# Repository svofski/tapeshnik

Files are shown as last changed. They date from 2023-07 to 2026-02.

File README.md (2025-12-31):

# Tapeshnik

Compact cassette data drive.

Project goals. Not all of them are realistic.

  * utilize an existing consumer tape mechanism with "logic control" to make a fully automatic tape drive
  * investigate the limits of what can be done with a simple compact cassette
  * implement random access to sectors
  * a usb mass storage device
  * use a stereo track for double data rate access, eventually use a 4-track head for quad data rate
  * investigate if altering motor speed to improve r/w speeds makes sense
  * investigate feasibility of reading while fast-forwarding with heads half-lifted

Eventually it's doomed to become either a dust gatherer/conversation piece or an art installation.

# Notes

There is no blog, but there are project notes, updated sometimes: [NOTES](docs/NOTES.md)

Note on the second iteration of Tapeshnik: [FUTURISTIC](docs/FUTURISTIC.md)

There is also a [youtube playlist](https://www.youtube.com/playlist?list=PLuOXWyWDhULNxkAvCRtwkEgnuxFfULnF9), where I try to show noteworthy things about this project. Like/subscribe!

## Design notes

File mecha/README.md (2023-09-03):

Mecha
~~~~~

This is an attempt to create a custom tape transport using available off the shelf parts, PCBs and 3d printed parts.

Useful projects and stuff
~~~~~~~~~~~~~~~~~~~~~~~~~

#### Mouse sensor PMW3389DM-T3QU + LM19-LSI

Breakout board https://github.com/siderakb/pmw3360-pcb

SROM
https://github.com/dkao/Kensington_Expert_Mouse_PMW3389_Arduino/blob/master/PMW3389DM-Mouse/SROM_PMW3389.ino

Recommended mouse sensors 
https://thegamingsetup.com/gaming-mouse/buying-guides/flawless-mouse-sensor-list

#### NopSCADlib mechanical parts for OpenSCAD

https://github.com/nophead/NopSCADlib

#### MG90S Servo Model

https://www.thingiverse.com/thing:253557

CAD files
~~~~~~~~~

Used cassette.step by Kai https://grabcad.com/kai-28. I adjusted Kai's design to match real world dimensions, hopefully.

There is no proper OpenSCAD model, although some parts are made using OpenSCAD before importing them into Blender. It's a complete mess that unfortunately can't be helped. Some mechanical OpenSCAD models use NopSCADlib.

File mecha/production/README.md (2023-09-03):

Files for printing

  bracket-l.stl			top cassette bracket left
  bracket-r.stl			top cassette bracket right
  narrow_flange.stl		flange for LM4UU bearing
  rear-bracket.stl		back bracket
  servobracket.stl		MG90S holding bracket
  spindle.stl			cassette spindle

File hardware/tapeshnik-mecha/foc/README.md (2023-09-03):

# TAPESHNIK MOTOR CONTROL

This is a dual-BLDC controller aimed at spinning two BLDC motors of a tape transport.

It is designed with SimpleFOC in mind.

Big thanks to SimpleFOC community for support, reviews and inspiration!

  Controller: 				Waveshare RP2040-Zero
  Motor drivers: 			STSPIN233
  Tape speed sensor:			PMW3389

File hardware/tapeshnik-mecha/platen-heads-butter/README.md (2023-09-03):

# TAPESHNIK Heads-Butter Platen

This is platen #3. The butter of the heads assembly sandwich.

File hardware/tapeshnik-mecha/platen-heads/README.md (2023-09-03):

# TAPESHNIK-MECHA Heads Platen

This is platen #2 of the TAPESHNIK-MECHA.

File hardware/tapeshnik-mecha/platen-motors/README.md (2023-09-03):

# TAPESHNIK Platen-Motors

This is platen #1 of TAPESHNIK-MECHA. It has the motors and the motor control board mounted behind them.

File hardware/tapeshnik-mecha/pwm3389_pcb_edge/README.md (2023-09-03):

# PWM3389-TAPESHNIK

This is a PWM3389 adapter board for use in TAPESHNIK. It is not intended for a general purpose mouse implementation.

The design is based on SideraKB's PMW3360-PCB https://github.com/siderakb/pmw3360-pcb

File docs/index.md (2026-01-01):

# TAPESHNIK 

Tapeshnik is a series of experiments with Compact Cassette tapes using a mix of traditional and modern technologies with focus on data storage.

## Iteration 1

Iteration 1 uses a purchased single-motor mechanism with a command wheel logic control. 
Read/Write circuitry is heavily based on Commodore datasette. Pi Pico is the microcontroller that does logic level data encoding/decoding and deck control functions.

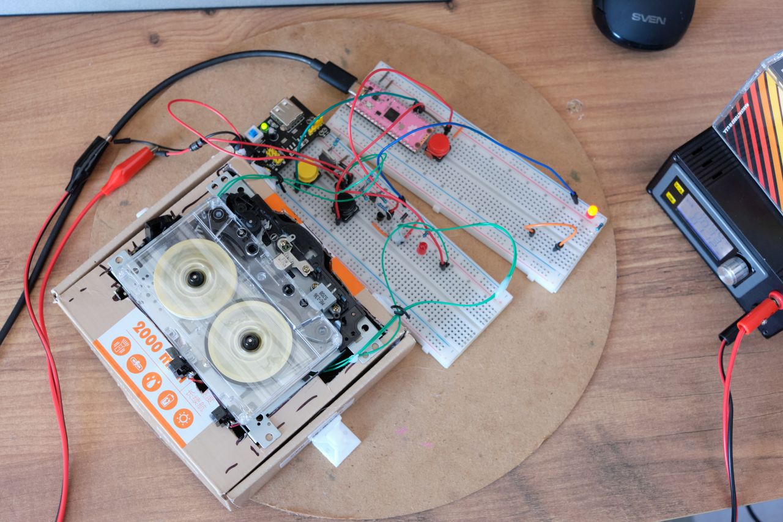
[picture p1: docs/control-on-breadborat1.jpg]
breadborat1


[Iteration 1 Notes](NOTES.md)

It was a moderate success, but not a breakthrough in data storage.

## Iteration 2

I always liked the idea of drives without rubber belts. Making a precision mechanism with a capstan can be a very demanding task. 
Some old data drives used to have no capstan, for example:

 * [Digital TU56 Dectape](https://gunkies.org/wiki/TU60_DECasetteTape_Transport)
 * [Digital TU60 DECassette](https://gunkies.org/wiki/TU60_DECasetteTape_Transport)
   * [Detailed description, principle of operation, data format of TU60](https://bitsavers.org/pdf/dec/decCassette/DEC-00-HTU60-C-D_TU60maint_Oct73.pdf)
 * Coleco Adam Digital Data Pack
 * [D/CAS drives](https://en.wikipedia.org/wiki/D/CAS)
 
Some of them use pre-recorded timing servo track, others appear to use robust encodings that let them recover data despite high tape speed variations.

This gave me ideas for a new experiment with building a fully custom deck without capstan.

mecha2025-2

This is currently a work in progress.

[Iteration 2 "FUTURISTIC" Notes](FUTURISTIC.md)

[youtube playlist](https://www.youtube.com/playlist?list=PLuOXWyWDhULNxkAvCRtwkEgnuxFfULnF9)

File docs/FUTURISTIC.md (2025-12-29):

# Tapeshnik Futuristic Notes

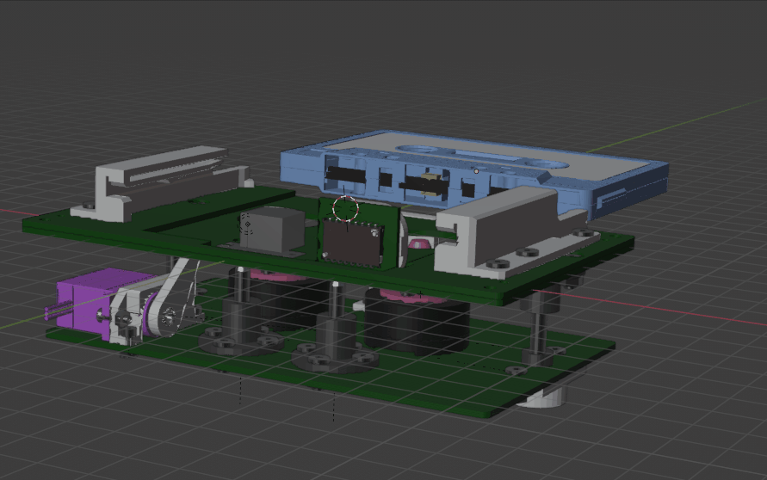
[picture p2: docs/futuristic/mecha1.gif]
mecha


While the current mechanism works, its limitations are obvious and its reliability is questionnable. Shall something break, it will be getting harder to get a replacement.

As a tangent project, I have an idea to design a simple, relatively easy to repeat tape mechanism that could be built from scratch using available parts. Obviously the heads will still have to be sourced, but cassette heads are relatively abundant.

As an inspiration I have TEAC D/CAS system. It uses tapes that look almost identical to Compact Cassettes. It's a two-motor direct drive system without a capstan. 

In D/CAS like TEAC MT-2ST, tape speed is closed-loop controlled by a closed loop servo, formed by the takeup reel motor and tape speed sensor. The tape speed sensor is not unlike a pinch roller, except that it does not pinch, instead rotates by friction with tape and provides speed reading.

Stable tape speed is useful, but depending on method of writing it may be not required. For example, a good PLL on FM or differential manchester can recover +-5% speed variation without issue, probably more with extra tweaks. But even better, if we sacrifice one of the tracks to reference clock signal, tape speed becomes almost a non-issue.

It's still worth researching sensing tape speed of course. Could a laser mouse sensor be used for that? In my past experiments, mice sensors experience frequent lapses which makes them useless for absolute position servo control. For speed sensing dropouts are also undesirable, but they may be a less significant problem.

The main frame of the mechanism can be built from several layers of PCB material stacked, connected via screws or standoffs. To insert a cassette it's necessary that some parts of the assembly move. We can either move the heads into the cassette, or motor spindles could be raised into the hubs when the cassette is inserted. I think the motors, or even just spindles, would be easier to move and the tolerances are much less tight for the spindles.

### RW heads

Ideally a 4-track head is needed. Erase head is not strictly necessary and a regular fixed autoreverse head would work.

### Motors

It's not 100% clear which kinds of motors are used in D/CAS, but at least some early versions used DC motors with speed controlled by current. That's cool but hard to match using off the shelf DC motors available today.

These days I think it's more practiccal to use BLDC motors. They are well researched and existing solutions for various kinds of BLDC control are available. Apparently we're looking for low-KV gimbal type motor, which should also be slotless to minimise cogging. An example of such a motor is JDPOWER MY-2813C, 75 yuan @ taobao. It seems to be slotless, although not with 100% certainty.

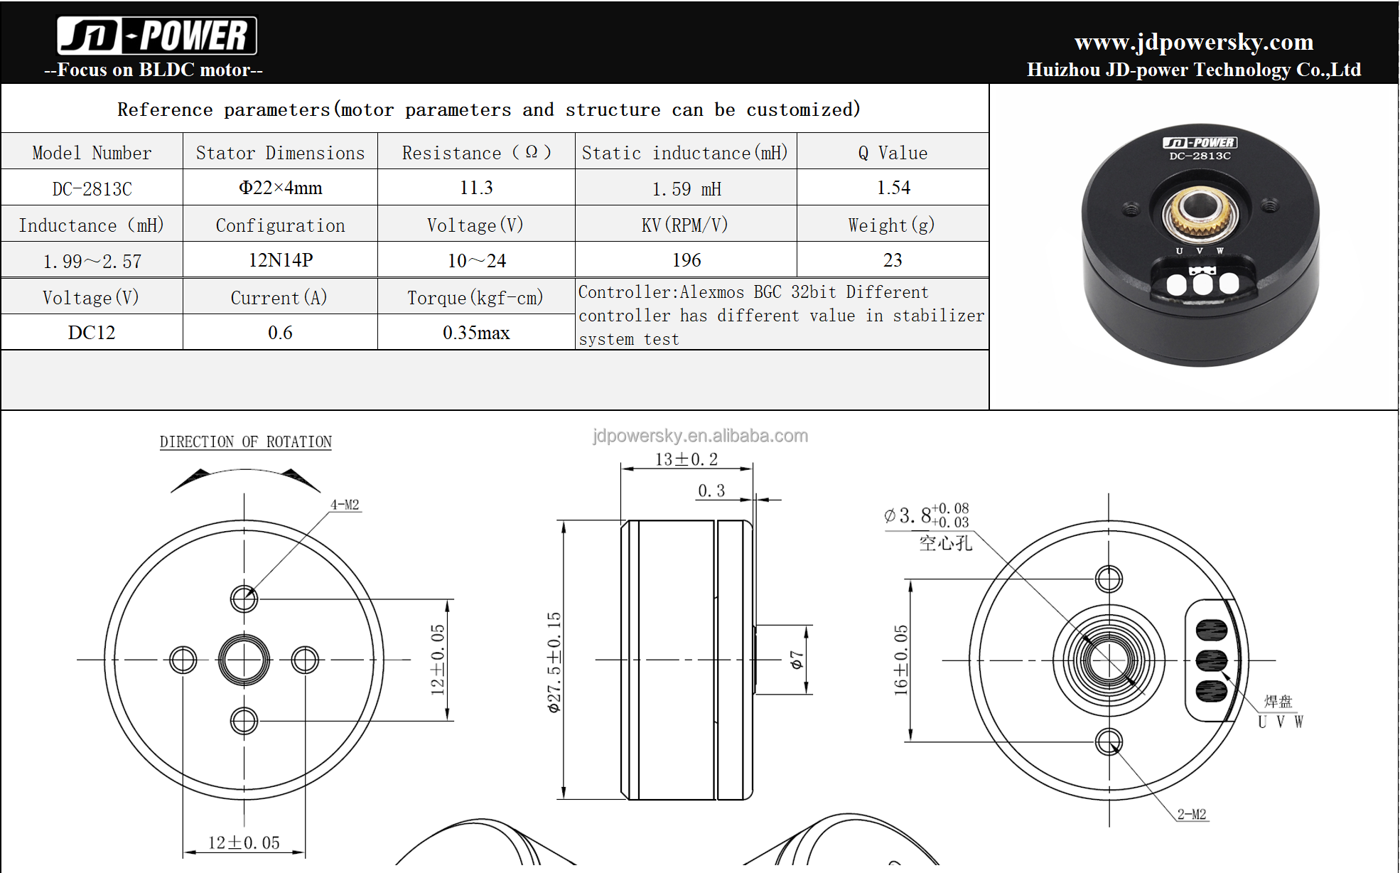
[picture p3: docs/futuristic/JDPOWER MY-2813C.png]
MY-2813C


It is also worth checking out if DVD motors can be used as well. They are not designed with small speed in mind, but they have ring magnets so they may cog less.

Motor controller board is going to use [SimpleFOC](https://simplefoc.com/).

Motor drivers: [STSPIN233](futuristic/stspin233-1.pdf)

### Sensor

List of "known good" mouse sensors from the point of view of gamers. 
https://thegamingsetup.com/gaming-mouse/buying-guides/flawless-mouse-sensor-list

A quick test shows that my random mouse at least sees the tape moving in the cassette. Worth investigating.

The sensor to be tested is [PMW3389DM-T3QU](futuristic/pixart_pmw3389dm-t3qu_-_productbrief_1374785_20.pdf)

### Standards

[STANDARD ECMA-34](futuristic/ECMA-34_3rd_edition_september_1976.pdf) has good technical drawings of D/CAS cassette. With the exception of the asymmetrical dent and lack of pressure pad, it's identical to Compact Cassette. I used this drawing as my reference:

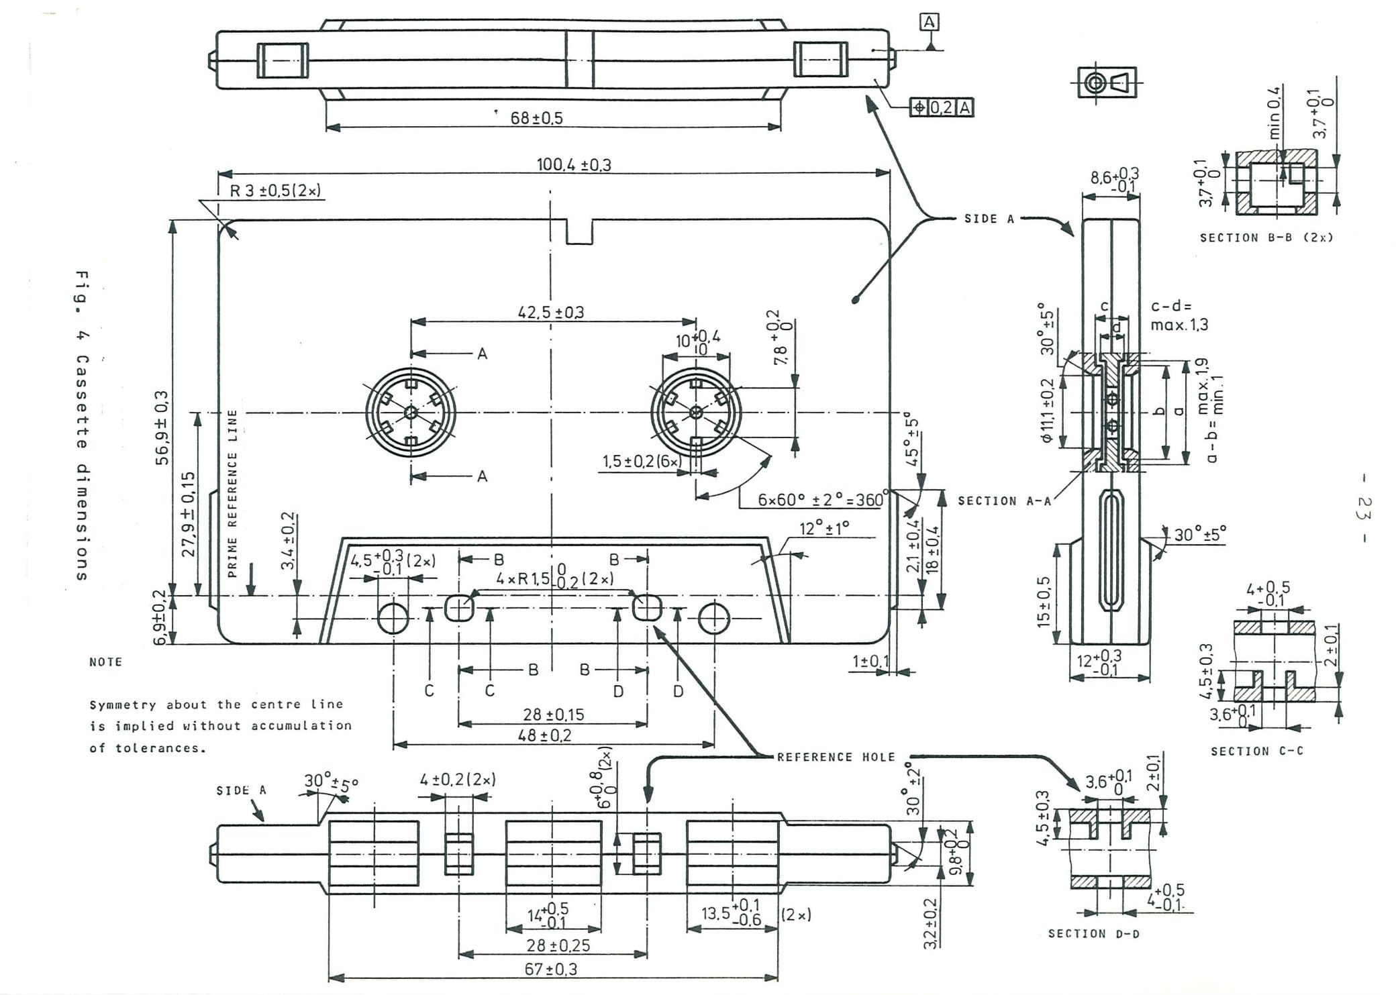
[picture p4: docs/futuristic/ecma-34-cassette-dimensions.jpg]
otherworldly beauty


### Update 08-DEC-2025

Here's a couple of pictures of the current state of the project:

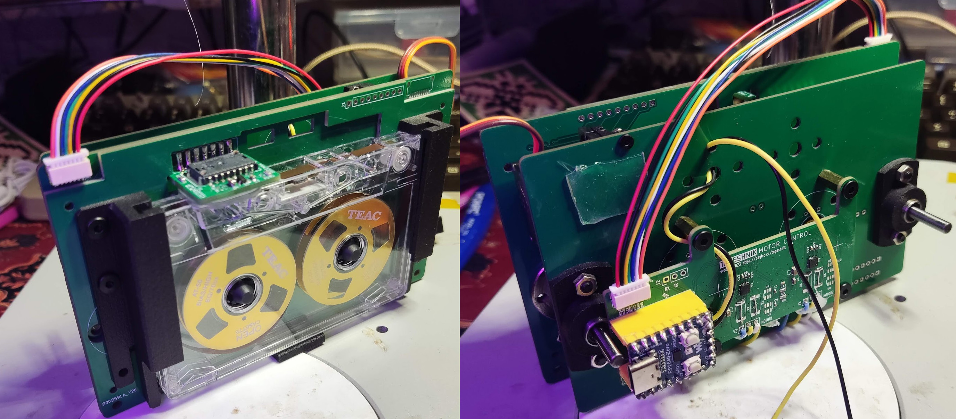
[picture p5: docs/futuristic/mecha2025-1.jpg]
mecha2025-1


Motors spinning

mecha2025-2

Both motors are controlled by RP2040-Zero for now, using SimpleFOC Arduino library using Philearlehower core. Only the basic control is implemented, something like PLAY/FF/REW/STOP. No tape travel speed estimation is done and the optical sensor is not yet used. 

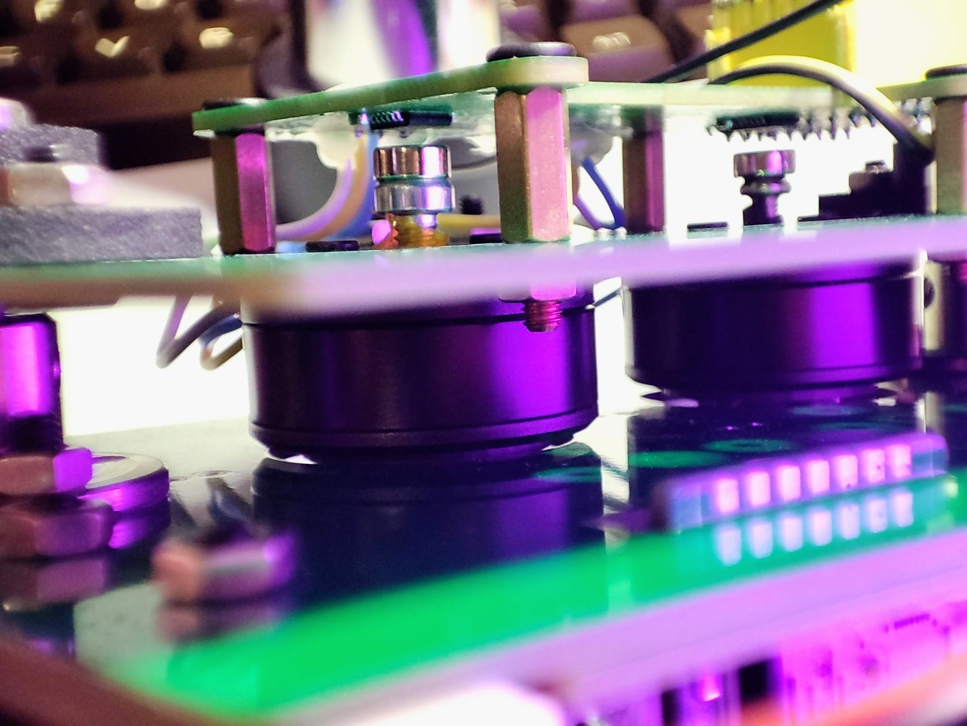
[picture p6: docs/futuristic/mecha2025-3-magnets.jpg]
mecha2025-3-magnets


My motors didn't have the encoder mounted and it turns out you can't just stick a magnet onto a hollow shaft and hope that it stays put. The shaft also has a rather weird 3.8mm inner diameter. I was able to find a couple of screws that stick in there reasonably well, but a more repeatable solution is needed.

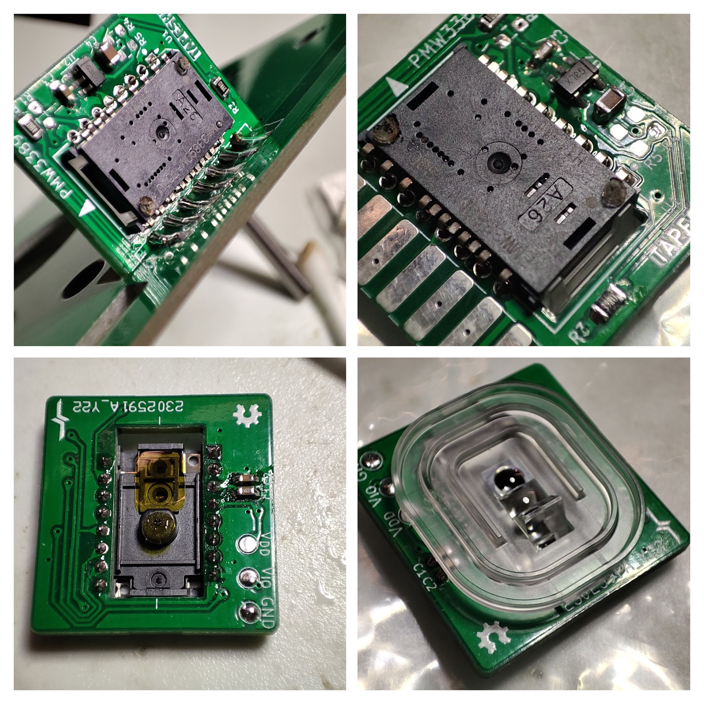
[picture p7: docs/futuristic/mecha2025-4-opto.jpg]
mecha2025-3-magnets


The optical chip PWM3389 is made using Vorlon technology. It seems to be tracking tape, time will tell how reliable it is.

Update: time did tell. The mouse sensor is not useful for tape tracking. SQUAL parameter can be used to detect tape leader, but the speed reading is highly variable and unpredictable. Update video link: [Tapeshnik Pt.6](https://www.youtube.com/watch?v=3gg_O02B6kA)

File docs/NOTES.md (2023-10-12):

# Tapeshnik

## ME-136 KS211M

### Mechanism Overview

ME-136 KS211M is a moniker for a logic controlled compact cassette mechanism sold in China.

ks211m-front
ks211m-back

ME-136 is the erase head. KS211M is Write/Playback head. The actual mechanism thus seems to have no name or part number. It is sold as new, but the belts seem to be weak from the start.

The only thing that's known is this little circuit diagram:

*THIS CIRCUIT IS HIGHLY SUSPECT!*

ks211m

 * Pin 0: not shown, not connected
 * Pin 1: write enable
 * Pin 2: mode wheel switch, open when the wheel reaches STOP position
 * Pin 3: control solenoid 12V (high-side switch)
 * Pin 4: GND
 * Pin 5: Photo interruptor output
 * Pin 6: Photo interruptor +5V
 * Pin 7: cassette detect

In reality the sensor board on my mechanism didn't have any resistors. I'm afraid I found it out too late. Maybe I damaged the photo sensor, or maybe it's some different thing entirely, but I'm replacing the sensor and changing the circuit to use a more sensible open-emitter connection. I removed the original sensor board and replaced it with this circuit using TCRT1000 reflective photo interruptor that I was able to find.
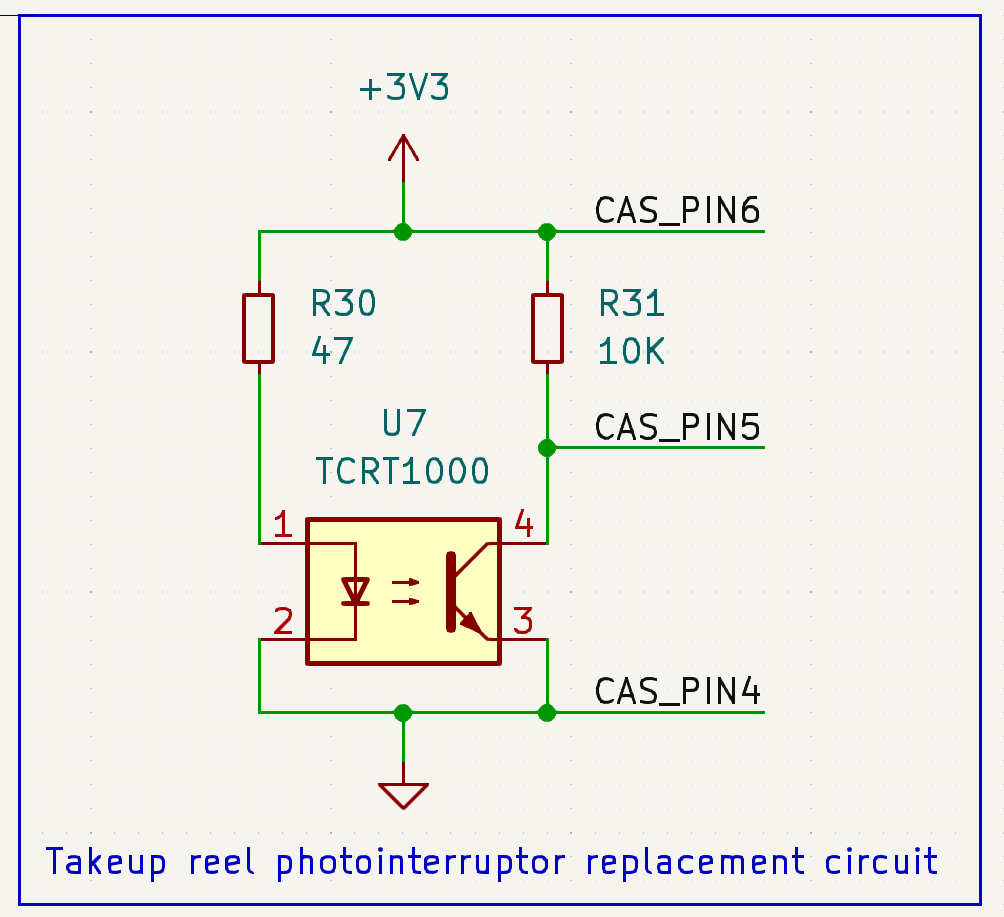
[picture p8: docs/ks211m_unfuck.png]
ks211munfuck


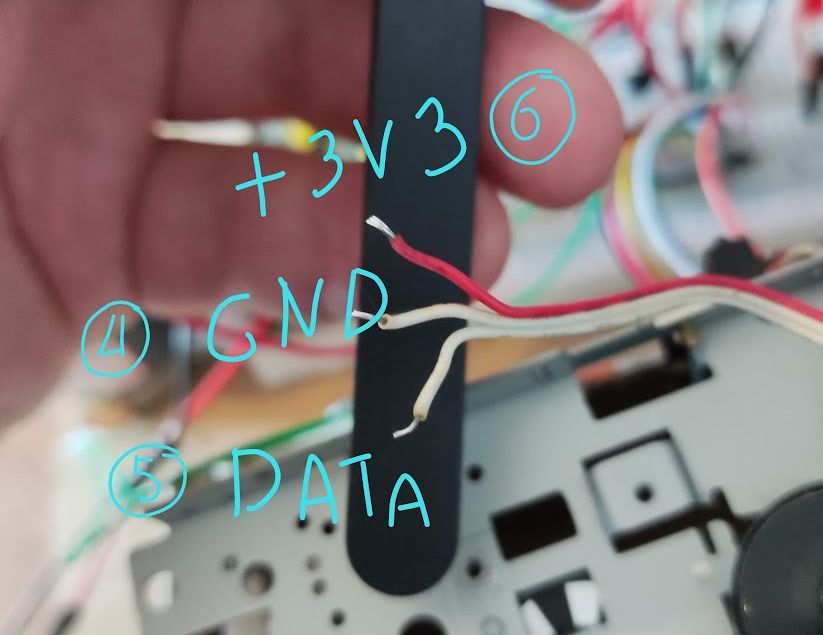
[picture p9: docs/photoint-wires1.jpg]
photoint-wires1

Here are the wires that go to the original sensor board, labeled.

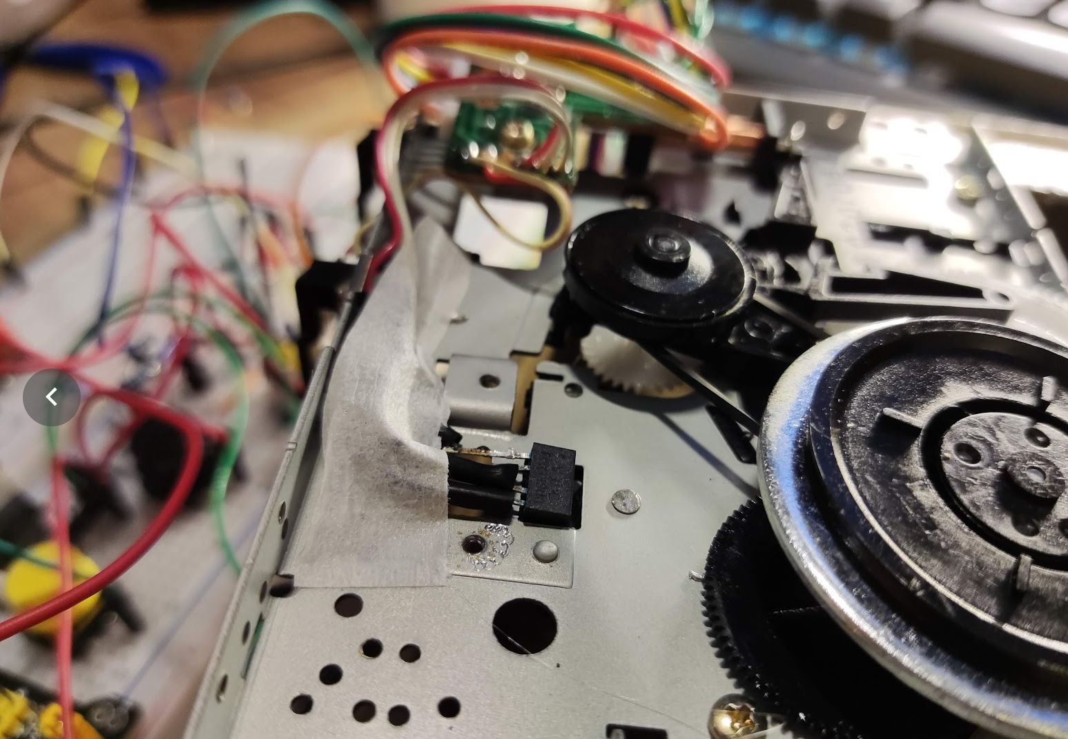
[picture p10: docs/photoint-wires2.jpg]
photoint-wires2

Photointerruptor with resistors hidden in the heat shrink tubes, tightly squeezed into the position of the old sensor board and reliably fixed in place.

reflective-wheel
The reflective sector wheel on the takeup reel. Monitoring it should help detecting when the tape is not moving and autostop must be engaged.

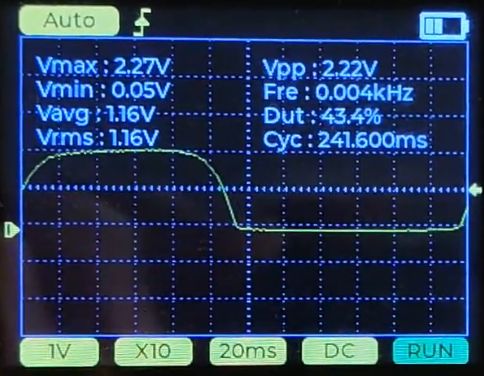
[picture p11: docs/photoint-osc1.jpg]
photoint-osc1

The signal on the phototransistor collector (connector pin 5 after modiifcation).

pin-numbers

I don't know the exact name of this kind of connector, but it has 2.0mm pitch and the cables can be bought, the search term is PH2.0MM间距端子线. For easy prototyping I removed the housing from the other end of the cable and soldered the contacts to a 2.54mm pin header.
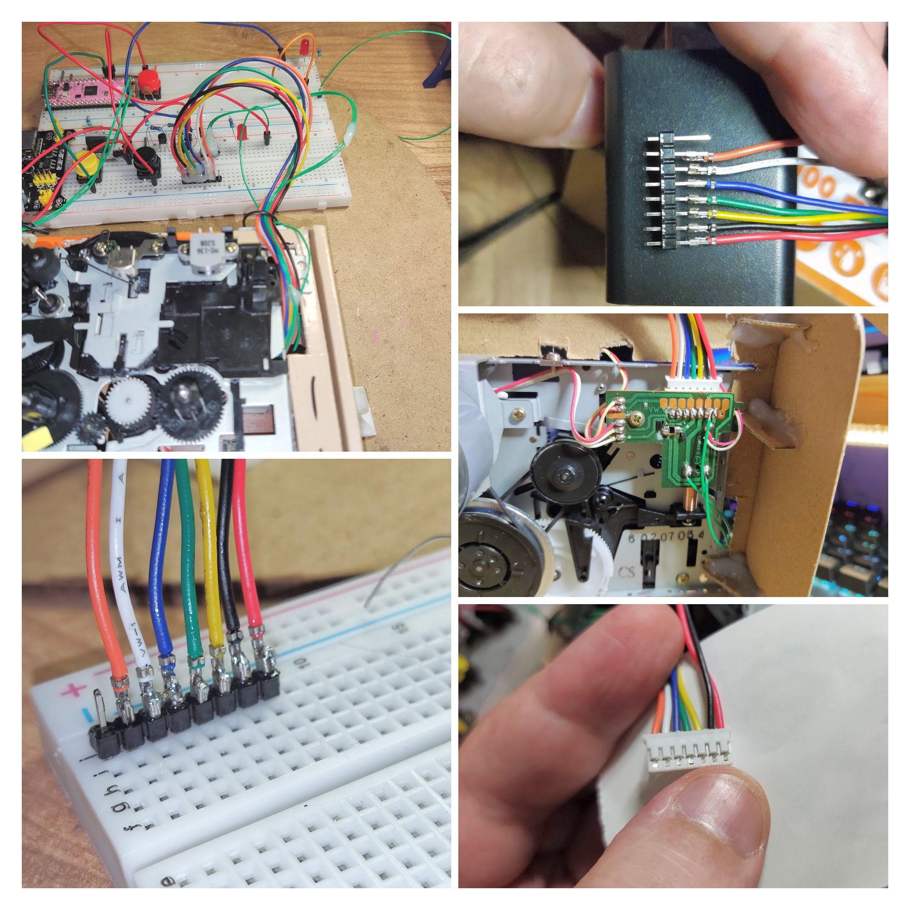
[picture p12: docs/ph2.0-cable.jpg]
cable connection


The motor pins are not on the main connector. It is a 12V DC motor. Connections on the motor are clearly marked "+" and "-". If my PSU is to be trusted, the motor alone consumes 0.045A at 12V in playback mode.

### Control

The mechanism modes are selected by pulsing the solenoid. The feeler arm follows the grooves on the command wheel and sets relevant parts of the mechanism in motion.

full-turn
The full turn of the command wheel takes approximately 900ms.

The wheel has 3 characteristic positions: 12 hours: STOP, 6 hours: PLAY, 10 hours: FF/REW.

The solenoid needs a pulse of about 10ms to begin state transition. Holding the pulse for longer is not necessary. It is possible that holding solenoid voltage works better than short pulses, I don't know which is the recommended mode of operation. Short pulses seem safer for the semiconductors.

#### Command wheel state transitions
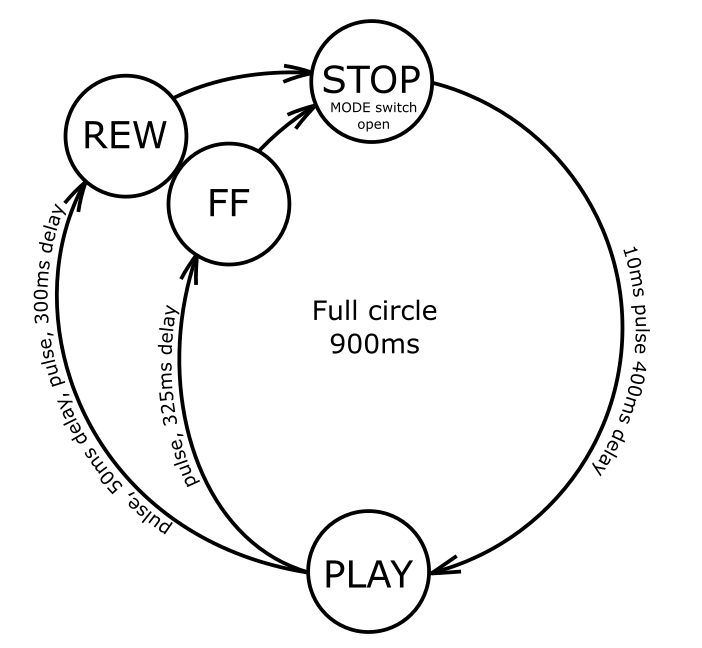
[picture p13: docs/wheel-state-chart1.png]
wheel-diagram

 * From STOP position, the first pulse will always put mechanism in PLAY position. 
 * From PLAY position, a single short pulse transitions to FF position.
 * From PLAY position, a short pulse + 50ms delay + a short pulse transitions to REW position.
 * From FF/REW any pulse transitions to STOP position.

#### Tachometer and autostop
This mechanism has no dedicated autostop sensor. The only way to implement autostop is by sensing rotation of the takeup reel. Same signal can also be used to implement a tape counter. A C60 cassette has approximately 13270 counts. The simple sensor has no way of telling rotation direction, so the counter tends to run away pretty quickly when there is a lot of back and forth with the tape. It should be possible to improve tracking by adding quadrature sensor like AEDR-8300.

Autostop is implemented with a help of a recurring timer. Every once in a while, a timer callback increments the counter. A tacho interrupt callback resets the counter. If the timer counter reaches certain value, e.g. 2, it means that it was not reset because the takeup reel is not spinning anymore and it's time to stop. This number would be different depending on fast / slow tape speed, but it also depends on where in the reel we are. A full spool near the end of tape spins slower.

Another safety mechanism is broken tape detection. An unusually quickly rotating takeup reel indicates that the tape is not held back by the capstan/pinch roller and is likely torn. The mechanism will also stop if unusually fast rotation is detected.

After a short while (1500ms) after full stop, the main motor is turned off.

#### Control conclusion

breadborat1

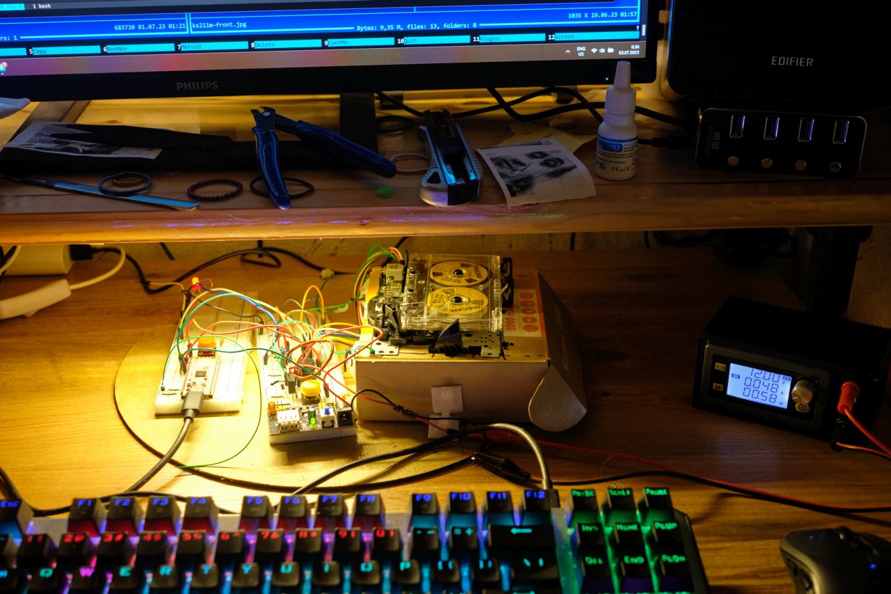
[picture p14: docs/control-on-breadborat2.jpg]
breadborat2


This could be built on a breadboard in a more compact way than I did it initially, but I transferred the working design to a protoyping board. I'm not the best when it comes to working on these things, but eventually I got the things right and the control circuit is now pretty solid. This opens up the way to work on the magnetic circuits.

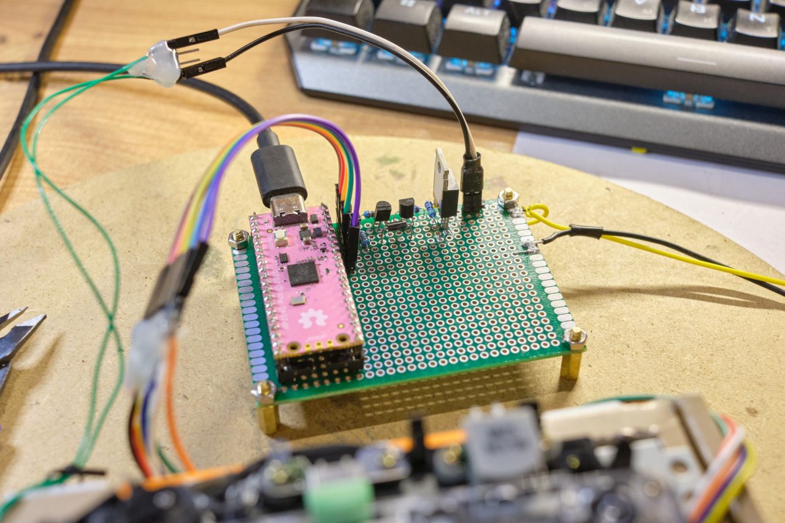
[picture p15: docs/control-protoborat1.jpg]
protoborat1


Video demo of motor control: https://www.youtube.com/watch?v=q-qPT_CDH74

### Magnetics

I'm expecting to get some results with this circuit that I copied from Commodore 1531 assembly version NP-090. Hopefully CD4052 will allow head commutation on the fly, if it does not, I'll have to find a better way.

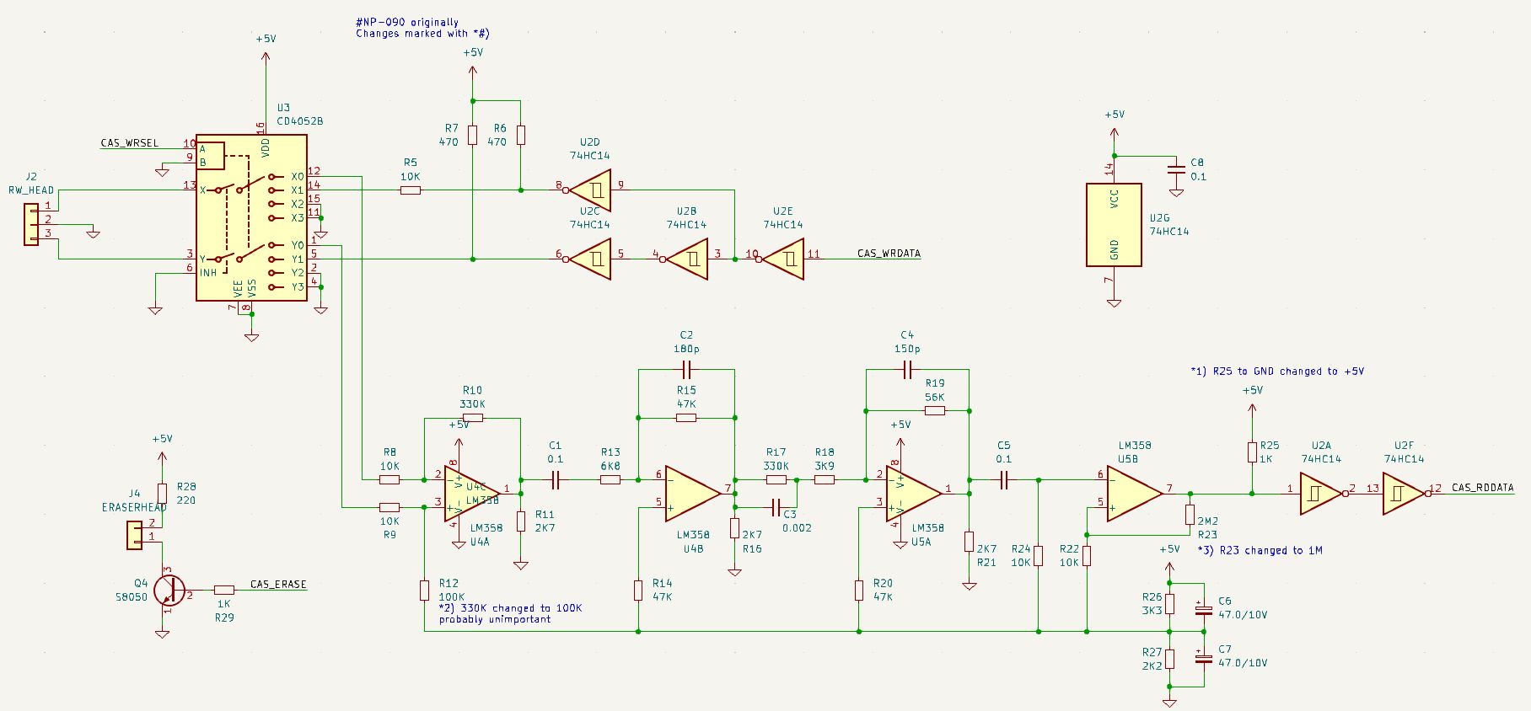
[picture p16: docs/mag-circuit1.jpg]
mag-circuit1


First writing experiment video: https://www.youtube.com/watch?v=b4VsjFtVbdQ

(Updated 23.07.23)

The circuit didn't work fully as expected, I had to troubleshoot it and make some changes. Video of troubleshooting process: https://www.youtube.com/watch?v=exBDKgd-HhU

Problems that I encountered:
  * low noise immunity: changed some routing on the breadboard, removed cd4052 for the time being, increased hysteresis
  * asymmetric waveform, 45-35% duty cycle instead of expected 50%. Changed R25 to pull up to +5 instead of GND

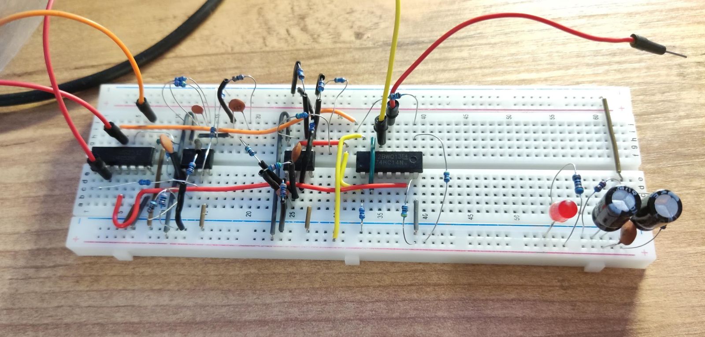
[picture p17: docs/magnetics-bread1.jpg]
magnetics1


Assembled amplifiers on the breadboard (before the debugging)

## Logic

Current goal: MFM. Example transport-level layout: 
  * leader sequence for PLL tune-up and to compensate for r/w switching and mechanical variance ~32 bytes
  * sync A1
  * 255 bytes data
      * 223 bytes payload
      * 32 bytes fec

Data payload layout:
  * track number [1]
  * sector number [3]
  * short copy of dirent: filename [12] + block number [4]
  * data [200]
  * crc-16 [2]
  * reserved [1]

Algorithm for writing sector number N+1:
  * locate sector N
  * read until the end
  * switch into write mode
  * write sector N+1

Or maybe should the sector marks be written once, leaving some small gaps for the rewrittable sections? In that case, for example

  * leader tone, A1, sector-number, A1, sector-number, A1, sector-number
  * long gap to fit the entire block of data, including the leader and its own sync sequence
  * next..

I've had some success in writing and reading data to tape, which is partly documented in the videos. Shortly after implementing soft head switching circuit using cd4052, I managed to cook my main work Pi Pico board. I don't know what exactly happened, probably a ground disconnect or something like that sent wrong voltage up GPIO pins. Curiously, the controller still works, but several GPIO pins don't function and it's abnormally warm to touch. While the board and new parts are in the post, it's time for a new hardware revision. I decided to take a break from tinkering and design a proper PCB. The design seems to be functional and I hope having a solid board with fewer dangling wires would make it easier to develop further. 

## Hardware revision 1

### Dealing with various voltages

Pi Pico is 3.3V, not 5V tolerant and we're dealing with 12V motor and solenoid plus 5V opamp circuits.

#### 12V

I redesigned +12V control circuits with a bit of a paranoid streak:

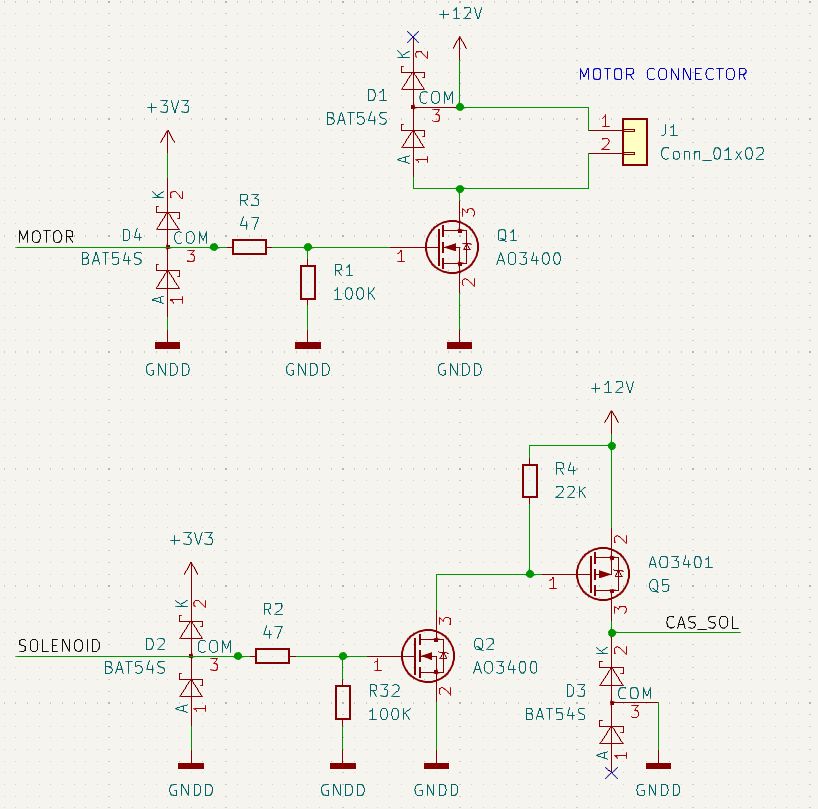
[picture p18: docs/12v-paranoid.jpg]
paranoid12v


The expectation is that if 12V would somehow leak back up GPIO side, the beefier BAT54S would withstand a larger current, and the current would be limited by R3 and R2.

Initially I used a lab supply to power the motor and solenoid, and USB bus power for everything else. This is ok for some tests, but it has become a bit too clunky. Also a catastrophic disconnect of a single wire could lead to my Pico getting cooked. So I decided to generate all voltages on board. 

To generate 12V, I want to use this DC-DC converter based on SX1308. 

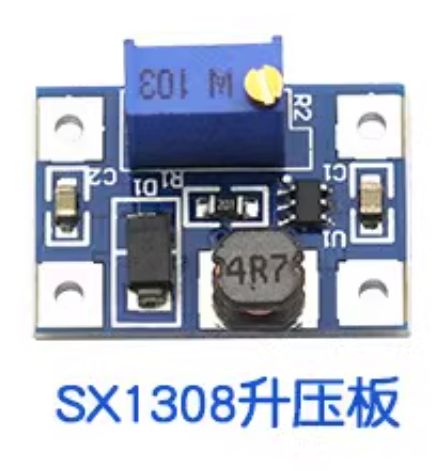
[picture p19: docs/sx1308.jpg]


The Chinese description says SX1308 DC-DC可调升压板2A, but it's unclear which part of it is taking 2A. It seems that it should be able to handle 12V/50mA needed by the motor. I'm a bit worried by solenoid, even though it's only used momentarily.

I only measured 4.5V on my USB bus power. This is not great for the analog section, so I decided to derive 5V with an LDO from the on-board generated 12V.

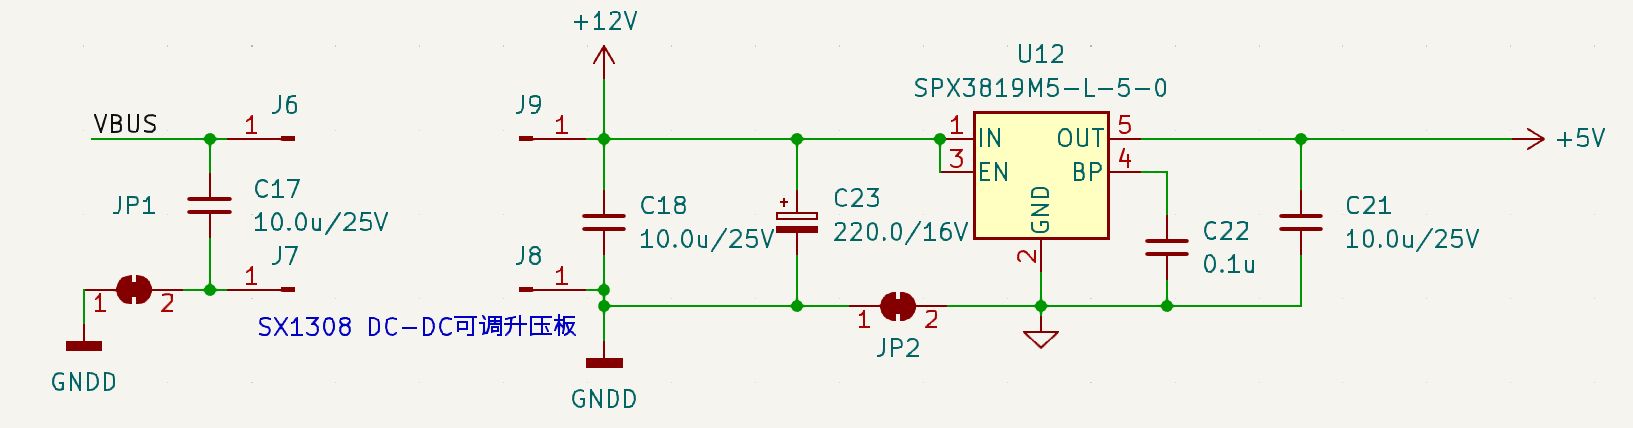
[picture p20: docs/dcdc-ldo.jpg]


Digital and analog grounds are separated. On PCB they join together at one point near the LDO.

There's a tap after the second stage of amplification that should in theory allow analog sampling of the signal. I'm really unsure about characteristics of the signal at this point, so there's an N/C resistor separating that part from ADC input pin. This part is not really in the current goals, but I wanted to leave something open for further experimentation here. Unfortunately I forgot to add clamp diodes on these pins too. Something to keep in mind.

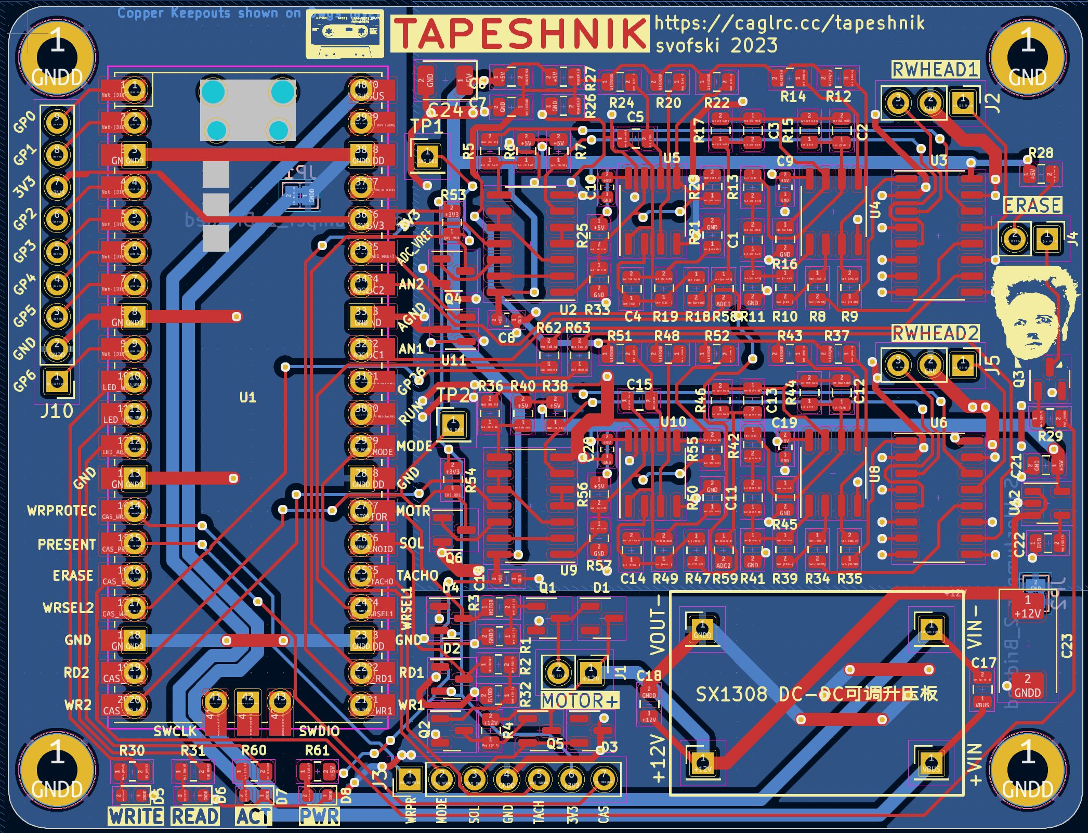
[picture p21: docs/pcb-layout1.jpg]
pcb layout


Waiting time...

And while we're waiting, it's time for the [FUTURISTIC](FUTURISTIC.md) TAPESHNIK-MECHA !

### Tapeshnik Proto 2

There was a couple of mistakes and some mishaps, but the new design seems to be good. I had to fix / bodge a couple of things.

#### Flipped p-MOSFET
The first one is a classic of course, forgot to flip p-MOSFET drawing in the high side switch circuit. This is what the fixed version looks like:

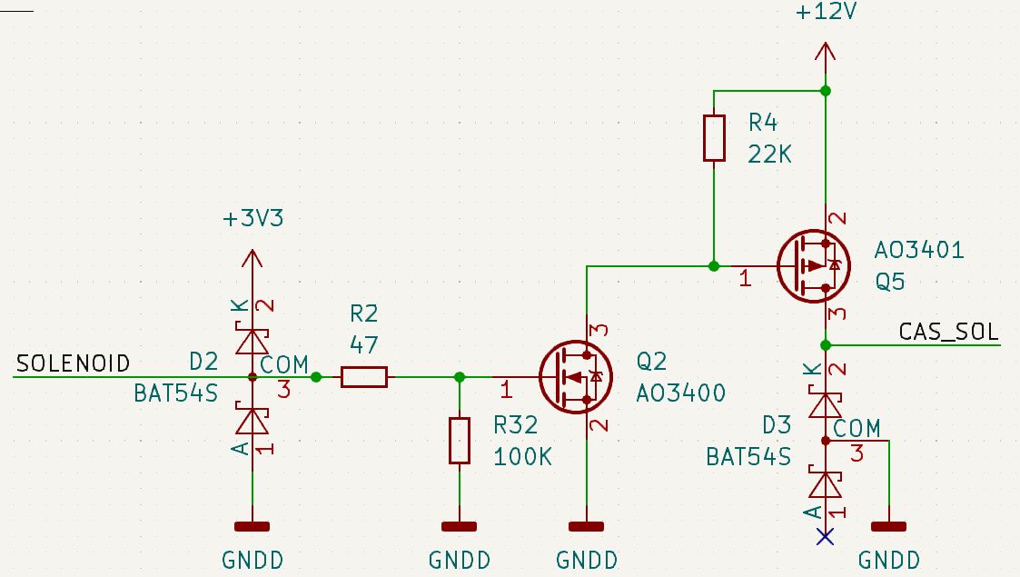
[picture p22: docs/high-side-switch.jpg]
high side mosfet


#### Power up inrush current
In this new version all power is provided by USB bus. Higher voltage neede by the motor and the solenoid is generated by a DC-DC converter. When the device is just plugged in, the inrush current may make the host think that something is not right with this device, cancel enumeration and shut down the port for protection. SX1308 chip has enable pin, but unfortunately on the modules that are sold everywhere, mine included, EN pin is dead shorted with Vin, so it can't be easily disabled. I didn't think this through at first, so I had to add this feature on a bodge. The circuit is like this:

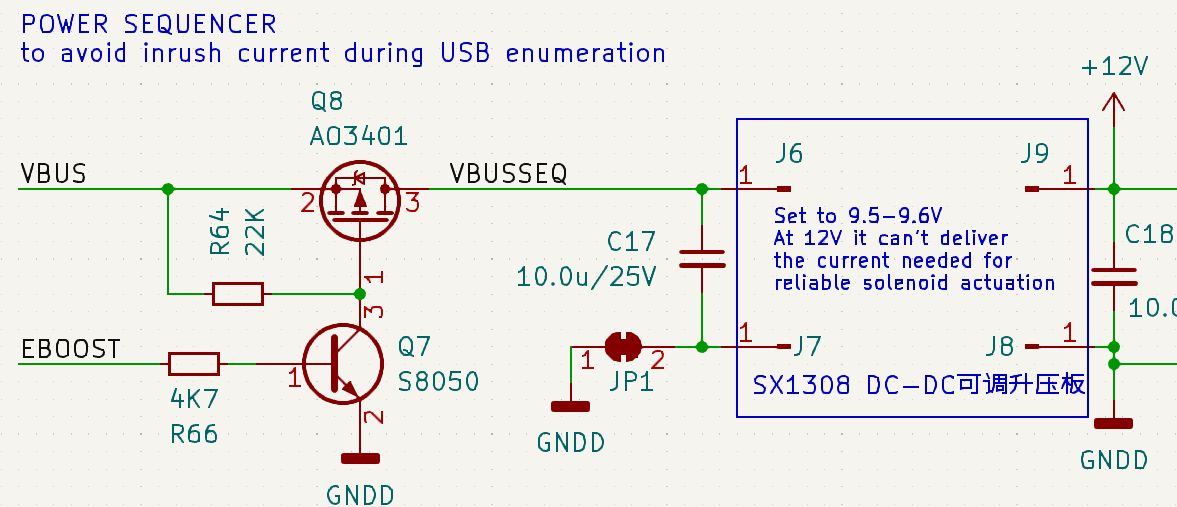
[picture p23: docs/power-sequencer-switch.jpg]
power sequencer switch


The additional benefit is that I can completely shut down the boost converter and go low power.

#### Weak DC-DC
SX1308 modules are described as "2A", but the reality is that they're not very efficient when boosting up to 12V. Here's a link to [Matt's Electronics](https://www.matts-electronics.com/wp-content/uploads/2018/06/SX1308.pdf) with a characterization of these modules and we can see that their efficiency takes a sharp nosedive at around 9-10V output when boosting up from 4.5-5V like I have here. This results in solenoid being very weak, I almost had to give it a helping hand sometimes. Luckily, both the motor and the solenoid work really well at 9.5V and at this voltage SX1308 is happy to push enough amperes. So my +12V is now +9.5V.

#### Continuing from where I left
There were some other mishaps not worthy of mention, mostly caused by my poor soldering and parts mishandling. 

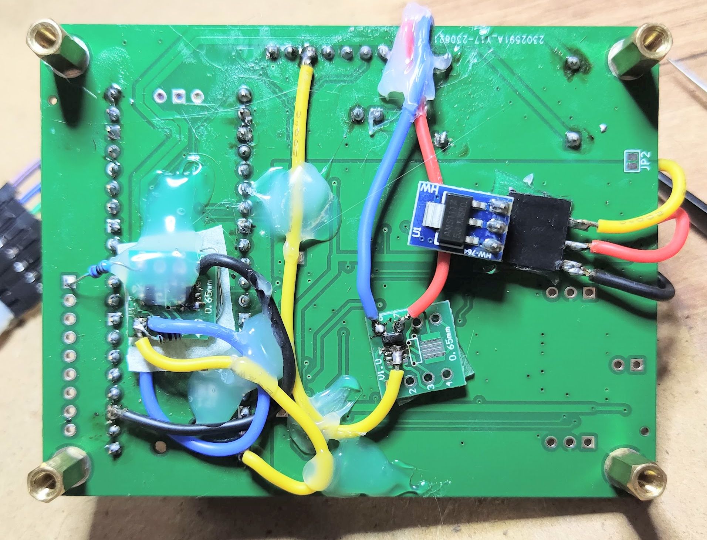
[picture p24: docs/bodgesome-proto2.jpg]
bodgesome board


After everything was sorted out, I managed to read the data from my cassette. 

[Tapeshnik is alive again (youtube short)](https://youtube.com/shorts/GOCvX2H30LI)

### Encoding, speed and errors

The new board with shielded cable to the heads work much better than my previous build. I've switched the encoding to MFM, although I'm not sure if it really performs better than FM. It seems that I can't reliably go beyond 700cps net. Which is a very respectable speed, but I feel that it could be better yet. Anything faster than that is prone to unrecoverable errors.

I performed successful sector data replacement tests. In the test I seek by reading sectors prior to the one that's to be replaced, switch into write mode and write new data. It works well, although I suspect that there is a misalignment caused by slight time deviations and eventually rewriting a sector might shift it, or other sectors. So I need a new sectoring scheme.

#### New sectoring scheme

The idea is to have sectors pre-recorded initially. Pre-recorded sector info will not be modified during normal operation. So the tape format is going to be like so:

  | SECTOR LEADER | SECTOR SYNC | SECTOR NUM x3 | PAYLOAD LEADER | PAYLOAD SYNC | PAYLOAD | rear gap |

This is very much like floppy disk format. Another level of matrioshka adds overhead, but it allows for a rigid sector structure that can be maintained in random-access usage.

It's possible to pack several payloads in one "physical" sector. Payload size is defined by libcorrect, it's 255 bytes, 223 of which are user data. One physical sector could contain one or more payloads, for example 4 seems like a reasonable compromise between sector length/time to seek and content size. Perhaps payloads within a sector could be block-interleaved for better resilience to long burst errors.

223 * 4 = 892 bytes

To plug this into Vector-06c MicroDOS, the sectors should be 1024 bytes long. The format is 80 tracks, 2 sides, 5 sectors. 223 * 5 = 1115, so 91 bytes or 8.2% wasted. Not great.
Or if we write it track by track, 223*23 = 5129 vs 1024*5 = 5120 --- that's a great match, but 23 blocks per record is a bit too much.

SECTOR SYNC and PAYLOAD SYNC should be different, for example:

  SECTOR SYNC: 1100110011000111  CCC7
  
  PAYLOAD SYNC:1100110011100011  CCE3

SECTOR NUM can be tripled for majority vote error correction.

#### Hardsectors update

Implemented the above scheme in "hardsectors" branch, merged to master. One sector is 4x FEC payloads, so 892 bytes. CRC is part of data and is counted for each subblock independently for the sake of simplicity. Sector rewriting works well. The only seeking method so far is linear reading until the sector is found.

There are several options to help seeks:

 * use tape counter to wind the tape approximately in position, then read linearly
 * use little spaces between sectors to count the sectors during ff/rew

The problem with tape counter as it is now is that it's fairly unreliable when changing tape direction. A definitive way would be replacing the sensor with a quadrature sensor. It's worth trying to understand the cause of this backlash and possibly compensate for it.

The spaces is something that sounds not very reliable because the head is not in full contact with the tape during ff/rew. It works for long pauses between songs, but probably not for sub-second pauses between sectors.

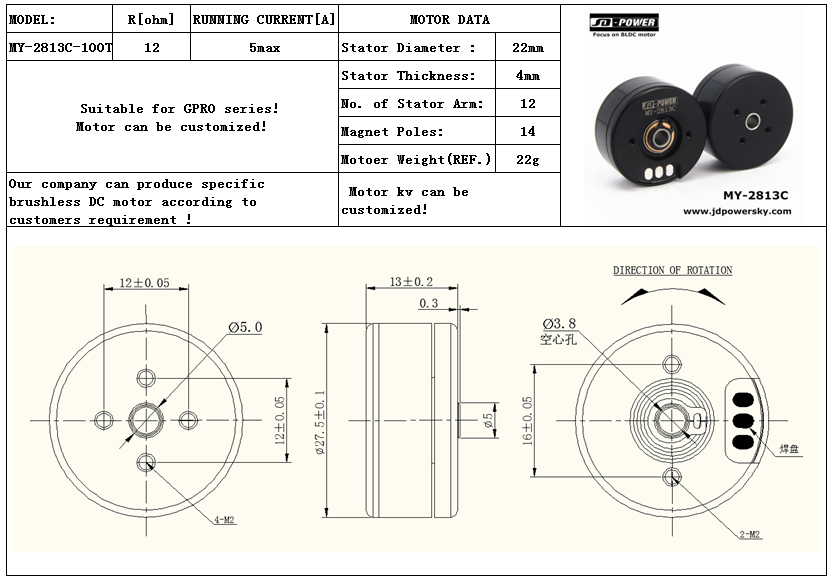
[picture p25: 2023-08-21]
docs/futuristic/pro1-1-text.jpg

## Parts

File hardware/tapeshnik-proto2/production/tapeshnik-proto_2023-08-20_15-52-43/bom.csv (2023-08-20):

Designator | Footprint | Quantity | Value | LCSC Part #
C1, C11, C15, C22, C5 | 0805 | 5 | 0.1u | C49678
C10, C16, C19, C20, C8, C9 | 0603 | 6 | 0.1u | C14663
C12, C2 | 0805 | 2 | 180p
C13, C3 | 0805 | 2 | 2000p
C14, C4 | 0805 | 2 | 150p
C17, C18, C21, C6, C7 | 0805 | 5 | 10.0u/25V
C23 | CP_EIA-7343-31_Kemet-D | 1 | 220.0/16V
C24 | CP_EIA-3528-21_Kemet-B | 1 | 47.0/16V
D1, D2, D3, D4 | SOT-23 | 4 | BAT54S
Q1, Q2, Q4, Q6 | SOT-23 | 4 | AO3400
Q3 | SOT-23 | 1 | S8050
Q5 | SOT-23 | 1 | AP3101
R1, R12, R32, R37 | 0805 | 4 | 100K
R10, R17, R39, R46 | 0805 | 4 | 330K
R11, R16, R21, R41, R45, R50 | 0805 | 6 | 2K7
R13, R42 | 0805 | 2 | 6K8
R14, R15, R20, R43, R44, R48 | 0805 | 6 | 47K
R18, R47 | 0805 | 2 | 3K9
R19, R49 | 0805 | 2 | 56K
R2, R3, R62, R63 | 0805 | 4 | 47
R22, R24, R34, R35, R36, R5, R51, R52, R8, R9 | 0805 | 10 | 10K
R23, R55 | 0805 | 2 | 2M2
R25, R29, R56 | 0805 | 3 | 1K
R26 | 0805 | 1 | 3K3
R27 | 0805 | 1 | 2K2
R28 | 0805 | 1 | 220
R30, R31, R38, R40, R6, R60, R7 | 0805 | 7 | 470
R33, R57, R58, R59 | 0805 | 4 | N/C
R4 | 0805 | 1 | 22K
R53, R54 | 0805 | 2 | 4K7
R61 | 0805 | 1 | 760

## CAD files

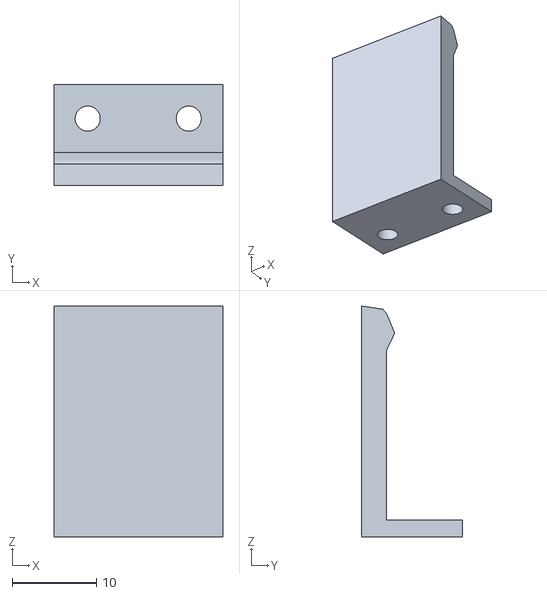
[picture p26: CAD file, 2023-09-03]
mecha/production/rear-bracket.stl
20.0 x 12.0 x 27.4

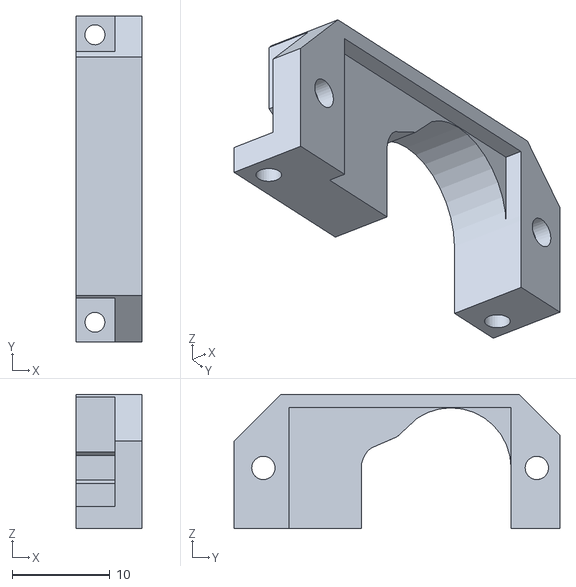
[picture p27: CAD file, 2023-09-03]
mecha/production/servobracket.stl
6.69 x 33.3 x 13.7

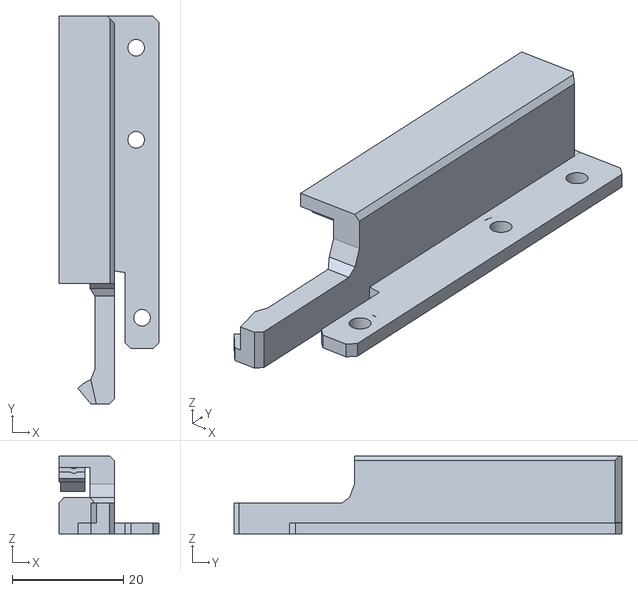
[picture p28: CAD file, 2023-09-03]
mecha/production/bracket-l.stl
18.0 x 69.8 x 14.0

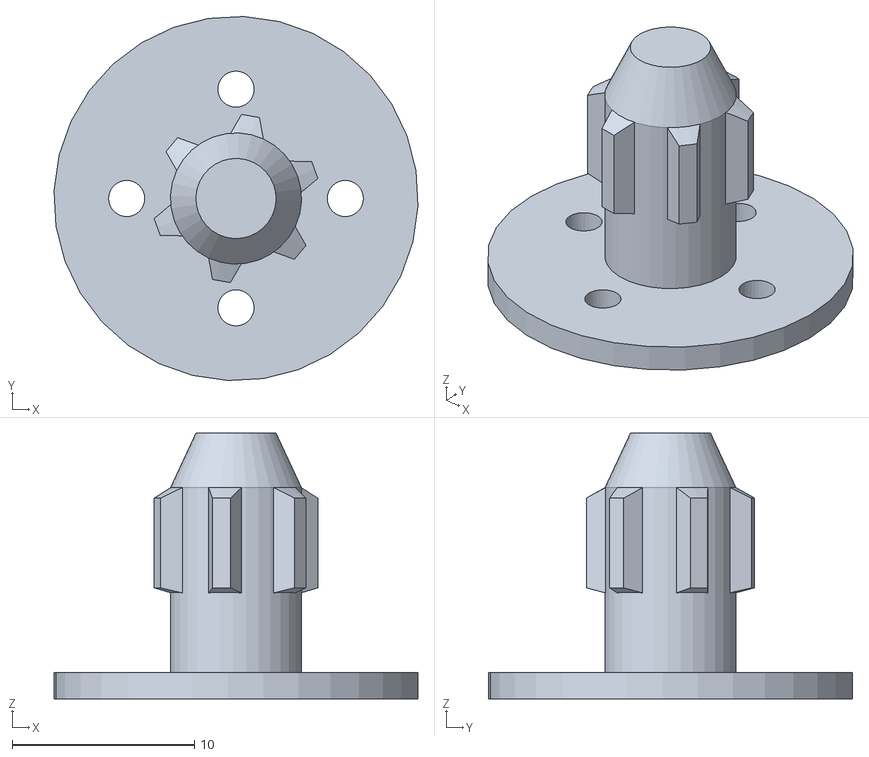
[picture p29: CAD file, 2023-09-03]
mecha/production/spindle.stl
20.0 x 20.0 x 14.6

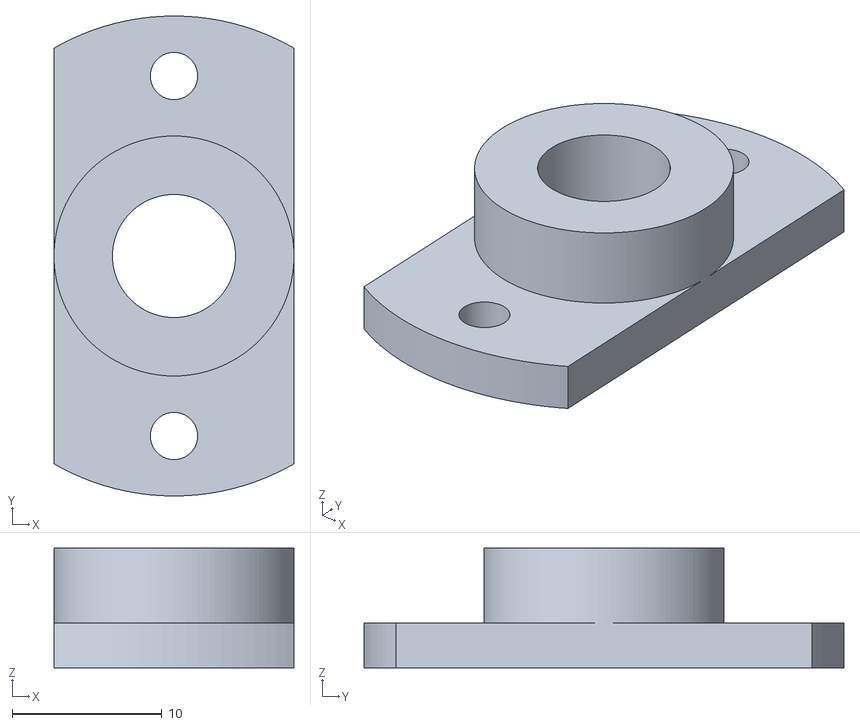
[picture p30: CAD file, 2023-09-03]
mecha/production/narrow_flange.stl
16.0 x 32.0 x 8.00

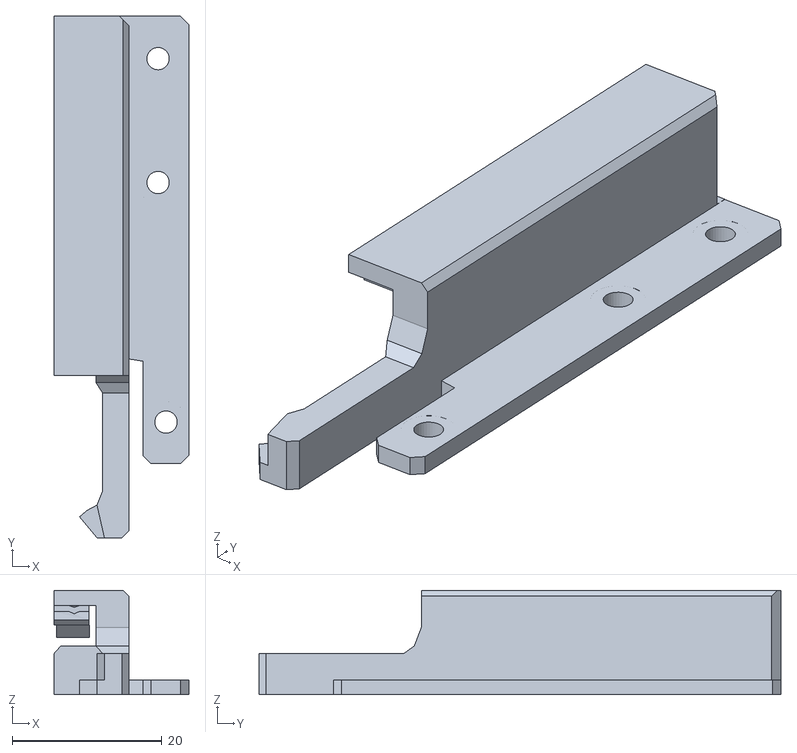
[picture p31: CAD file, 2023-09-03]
mecha/production/bracket-r.stl
18.0 x 69.8 x 14.0

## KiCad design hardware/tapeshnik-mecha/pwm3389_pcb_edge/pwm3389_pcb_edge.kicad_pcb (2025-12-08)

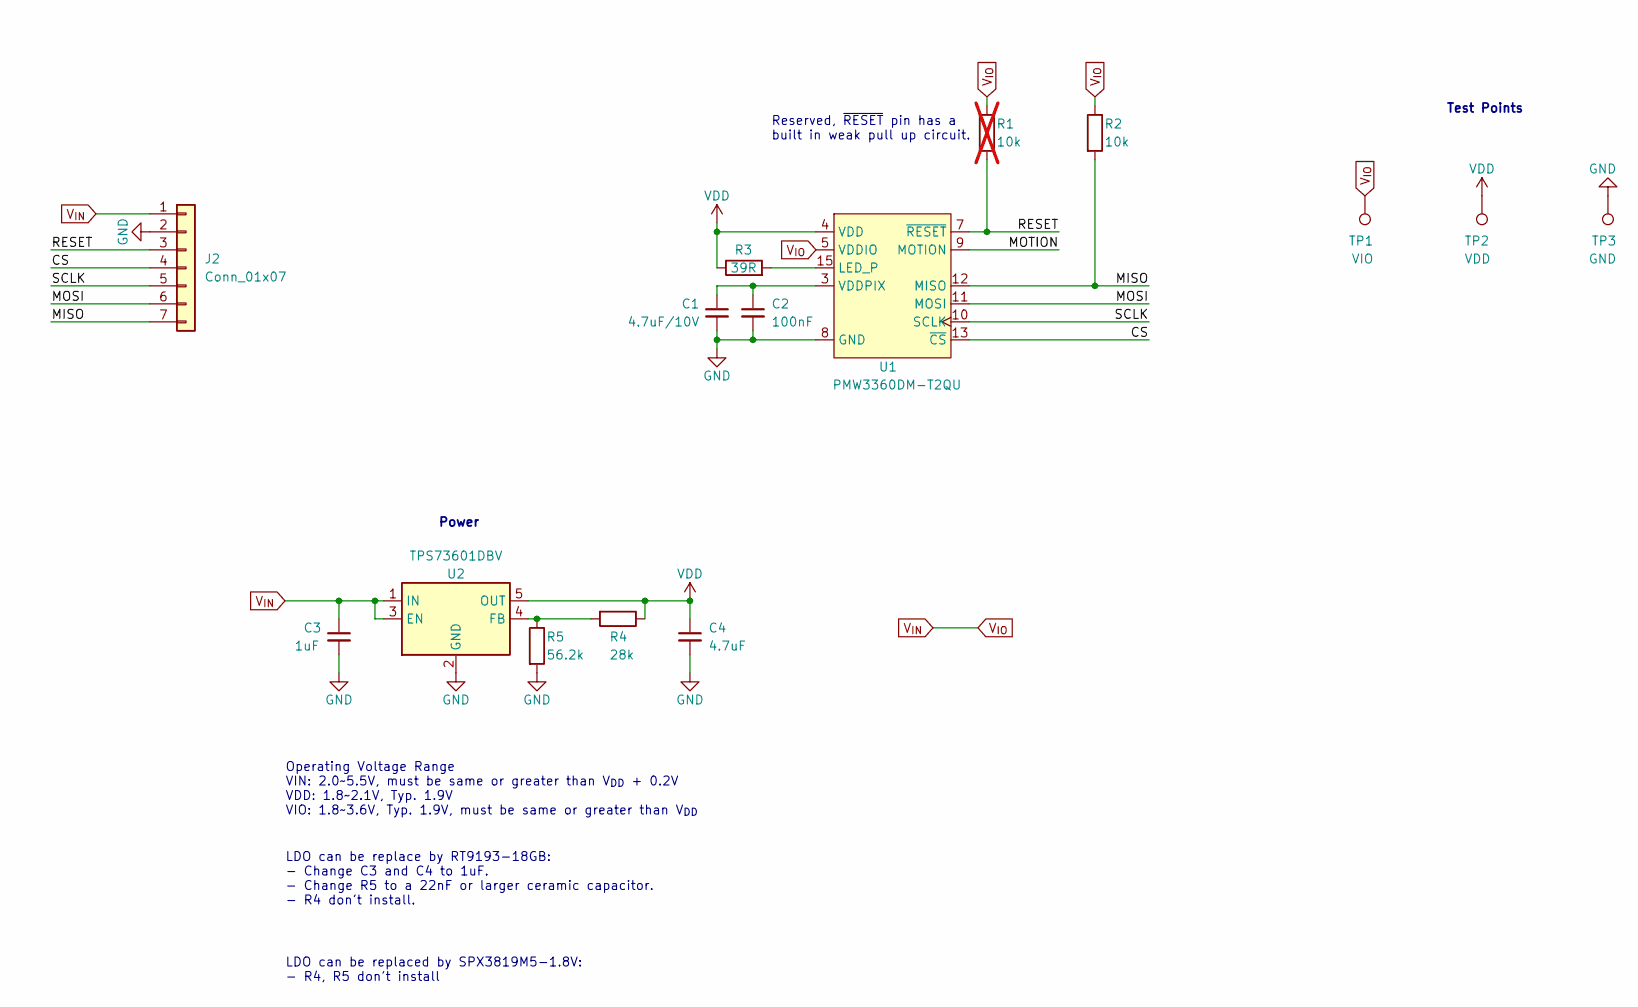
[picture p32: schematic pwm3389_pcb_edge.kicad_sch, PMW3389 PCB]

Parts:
C1: 4.7uF/10V; C_0603_1608Metric_Pad1.08x0.95mm_HandSolder
C2: 100nF; C_0603_1608Metric_Pad1.08x0.95mm_HandSolder
C3: 1uF; C_0603_1608Metric_Pad1.08x0.95mm_HandSolder
C4: 4.7uF; C_0603_1608Metric_Pad1.08x0.95mm_HandSolder
J2: Conn_01x07; EDGE-2.54-7x
R1: 10k; R_0603_1608Metric_Pad0.98x0.95mm_HandSolder; not fitted
R2: 10k; R_0603_1608Metric_Pad0.98x0.95mm_HandSolder
R3: 39R; R_0603_1608Metric_Pad0.98x0.95mm_HandSolder
R4: 28k; R_0603_1608Metric_Pad0.98x0.95mm_HandSolder
R5: 56.2k; R_0603_1608Metric_Pad0.98x0.95mm_HandSolder
TP1: VIO; TestPoint_Pad_D1.5mm
TP2: VDD; TestPoint_Pad_D1.5mm
TP3: GND; TestPoint_Pad_D1.5mm
U1: PMW3360DM-T2QU; PMW3360DM-T2QU 16Pin
U2: TPS73601DBV; SOT-23-5

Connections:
/CS: J2.4, U1.13 (~CS)
/MISO: J2.7, R2.2, U1.12 (MISO)
/MOSI: J2.6, U1.11 (MOSI)
/MOTION: U1.9 (MOTION)
/RESET: J2.3, R1.2, U1.7 (~RESET)
/SCLK: J2.5, U1.10 (SCLK)
GND: C1.2, C2.2, C3.2, C4.2, J2.2, R5.2, TP3.1, U1.8 (GND), U2.2 (GND)
unnamed: R3.2, U1.15 (LED_P)
unnamed: C1.1, C2.1, U1.3 (VDDPIX)
unnamed: R4.2, R5.1, U2.4 (FB)
VDD: C4.1, R3.1, R4.1, TP2.1, U1.4 (VDD), U2.5 (OUT)
V_{IN}: C3.1, J2.1, R1.1, R2.1, TP1.1, U1.5 (VDDIO), U2.1 (IN), U2.3 (EN)

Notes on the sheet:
Reserved, ~{RESET} pin has a built in weak pull up circuit.
LDO can be replaced by SPX3819M5-1.8V: - R4, R5 don't install
Operating Voltage Range VIN: 2.0~5.5V, must be same or greater than V_{DD} + 0.2V VDD: 1.8~2.1V, Typ. 1.9V VIO: 1.8~3.6V, Typ. 1.9V, must be same or greater than V_{DD}
LDO can be replace by RT9193-18GB: - Change C3 and C4 to 1uF. - Change R5 to a 22nF or larger ceramic capacitor. - R4 don't install.
Test Points
Power

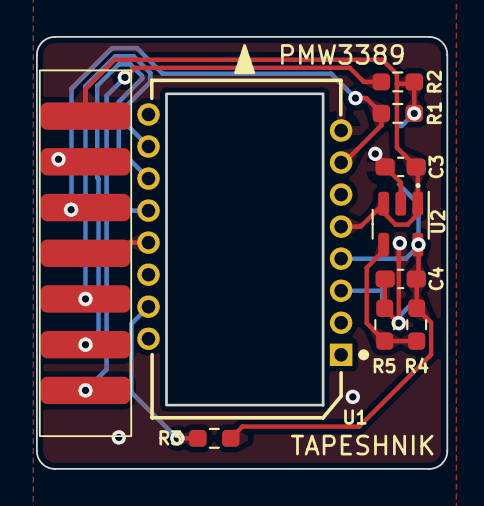
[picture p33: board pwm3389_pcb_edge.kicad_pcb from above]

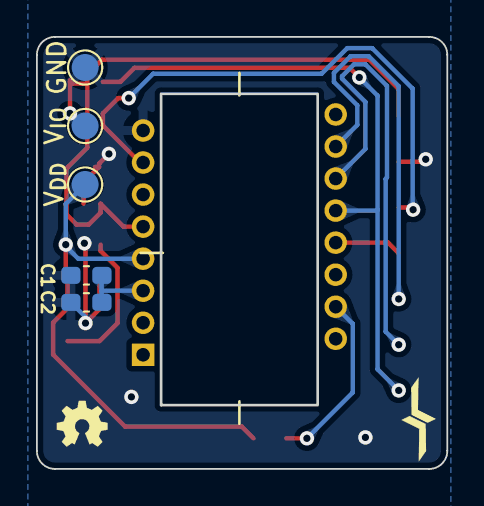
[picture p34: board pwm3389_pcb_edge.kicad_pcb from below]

Board: 2 copper layers, 22.8 x 24.0 mm, 15 parts (5 on the bottom side), 11 nets.

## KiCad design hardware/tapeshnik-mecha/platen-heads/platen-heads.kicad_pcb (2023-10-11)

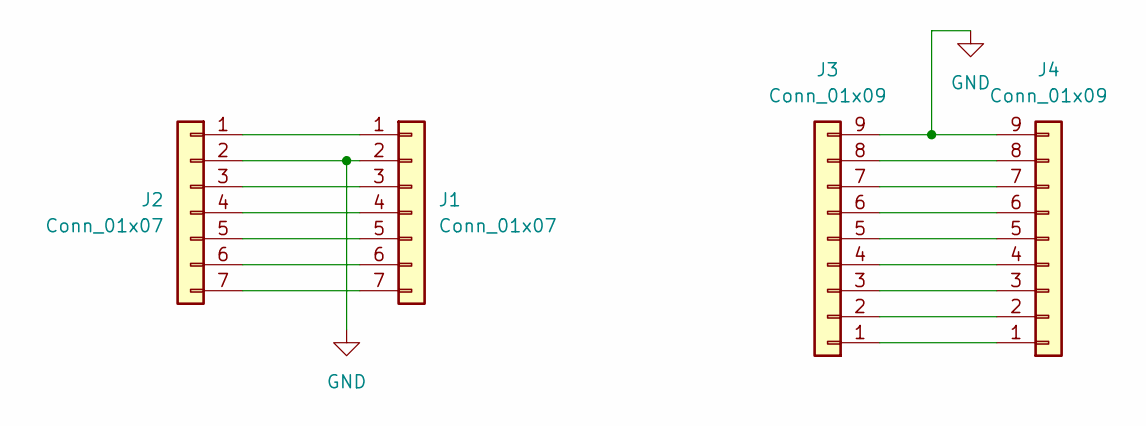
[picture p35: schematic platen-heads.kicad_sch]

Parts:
J1: Conn_01x07; EDGE-2.54-7x
J2: Conn_01x07; JST_SH_SM07B-SRSS-TB_1x07-1MP_P1.00mm_Horizontal
J3: Conn_01x09; JST_SH_SM09B-SRSS-TB_1x09-1MP_P1.00mm_Horizontal
J4: Conn_01x09; PinHeader_1x09_P2.54mm_Vertical

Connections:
GND: J1.2, J2.2, J3.9, J4.9
unnamed: J1.1, J2.1
unnamed: J1.3, J2.3
unnamed: J1.4, J2.4
unnamed: J1.5, J2.5
unnamed: J1.6, J2.6
unnamed: J1.7, J2.7
unnamed: J3.1, J4.1
unnamed: J3.2, J4.2
unnamed: J3.3, J4.3
unnamed: J3.4, J4.4
unnamed: J3.5, J4.5
unnamed: J3.6, J4.6
unnamed: J3.7, J4.7
unnamed: J3.8, J4.8

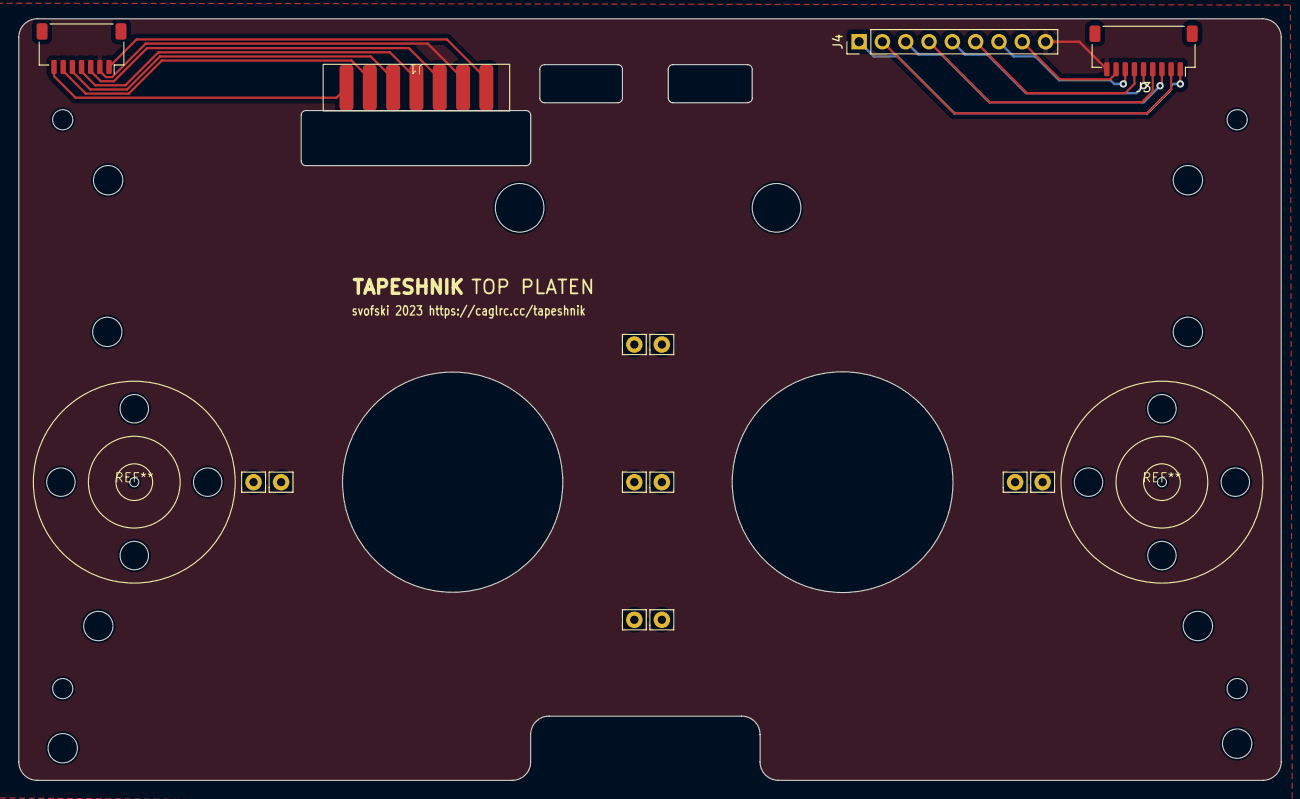
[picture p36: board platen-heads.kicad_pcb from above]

Board: 2 copper layers, 137.6 x 83.0 mm, 4 parts (0 on the bottom side), 15 nets.

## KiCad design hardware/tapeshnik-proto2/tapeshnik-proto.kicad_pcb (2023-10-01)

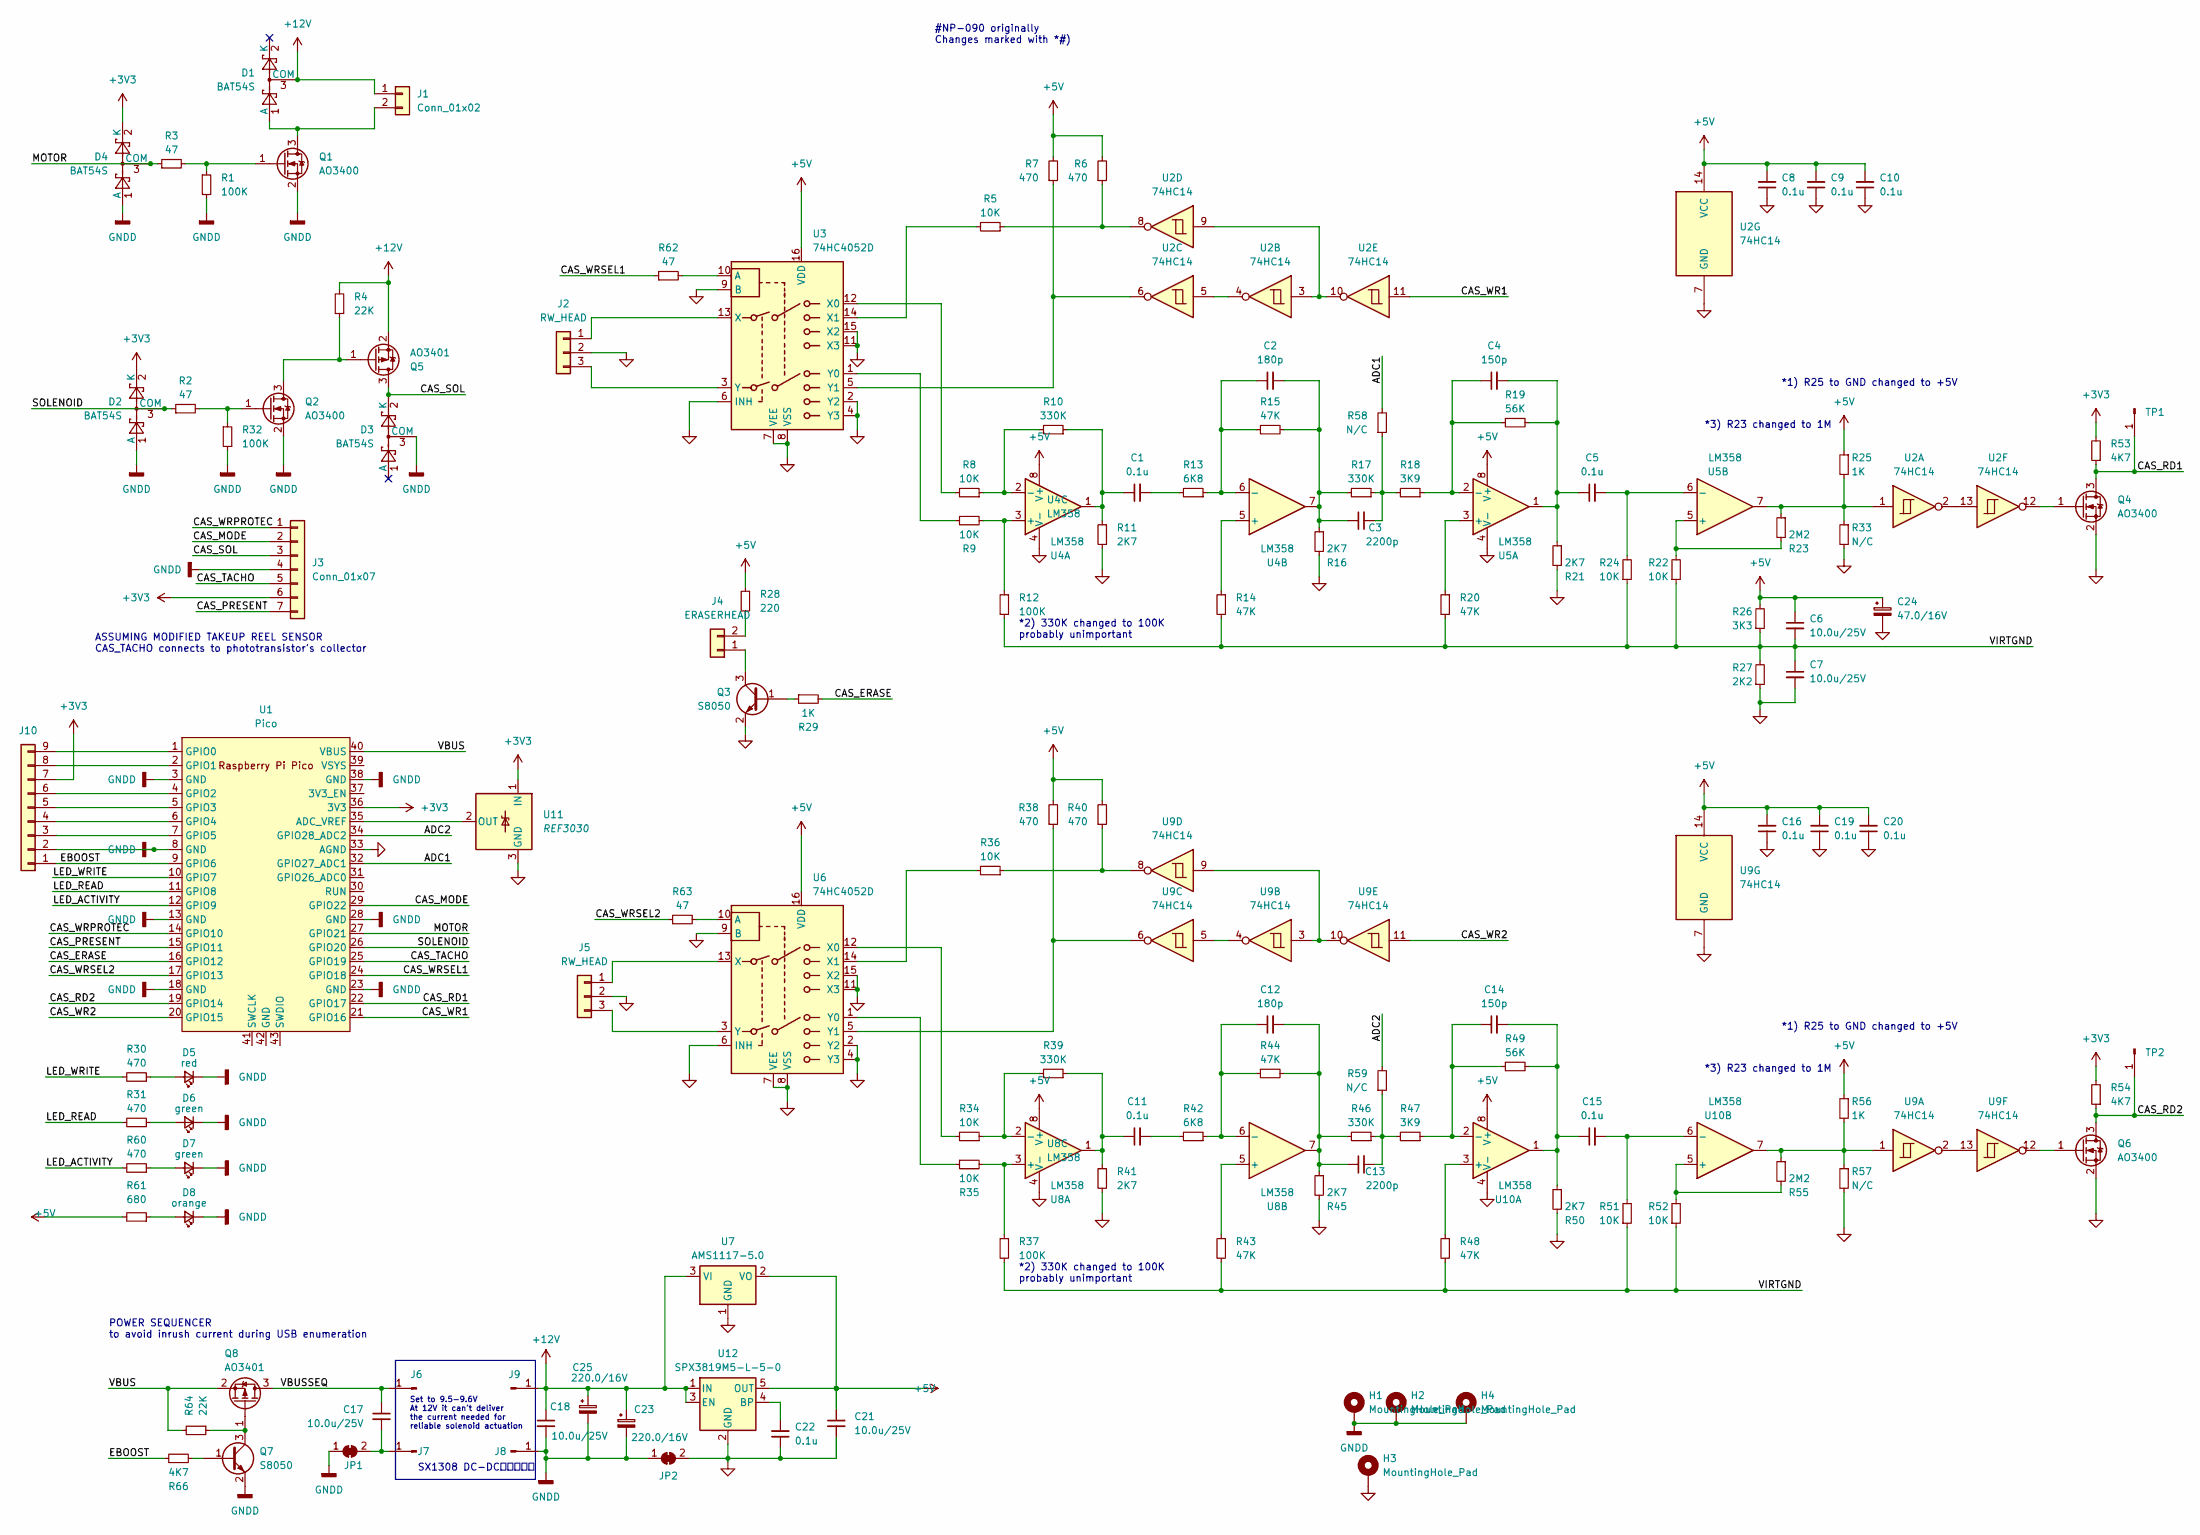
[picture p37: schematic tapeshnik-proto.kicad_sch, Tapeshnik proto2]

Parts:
C1, C5, C11, C15, C22: 0.1u; C_0805_2012Metric; LCSC C49678
C2, C12: 180p; C_0805_2012Metric
C3, C13: 2200p; C_0805_2012Metric; LCSC C28260
C4, C14: 150p; C_0805_2012Metric
C6, C7, C17, C18, C21: 10.0u/25V; C_0805_2012Metric
C8, C9, C10, C16, C19, C20: 0.1u; C_0603_1608Metric; LCSC C14663
C23, C25: 220.0/16V; CP_EIA-7343-31_Kemet-D
C24: 47.0/16V; CP_EIA-3528-21_Kemet-B
D1, D2, D3, D4: BAT54S; SOT-23
D5: red; LED_0603_1608Metric
D6, D7: green; LED_0603_1608Metric
D8: orange; LED_0603_1608Metric
H1, H2, H3, H4: MountingHole_Pad; MountingHole_3.2mm_M3_DIN965_Pad
J1: Conn_01x02; PinHeader_1x02_P2.54mm_Vertical
J2, J5: RW_HEAD; PinHeader_1x03_P2.54mm_Vertical
J3: Conn_01x07; PinHeader_1x07_P2.54mm_Vertical
J4: ERASERHEAD; PinHeader_1x02_P2.54mm_Vertical
J6, J7, J8, J9: Conn_01x01_Pin; PinHeader_1x01_P2.54mm_Vertical
J10: Conn_01x09; PinHeader_1x09_P2.54mm_Vertical
JP1, JP2: SolderJumper_2_Bridged; SolderJumper-2_P1.3mm_Bridged2Bar_Pad1.0x1.5mm
Q1, Q2, Q4, Q6: AO3400; SOT-23
Q3, Q7: S8050; SOT-23
Q5, Q8: AO3401; SOT-23
R1, R12, R32, R37: 100K; R_0805_2012Metric
R2, R3, R62, R63: 47; R_0805_2012Metric
R4, R64: 22K; R_0805_2012Metric
R5, R8, R9, R22, R24, R34, R35, R36, R51, R52: 10K; R_0805_2012Metric
R6, R7, R30, R31, R38, R40, R60: 470; R_0805_2012Metric
R10, R17, R39, R46: 330K; R_0805_2012Metric
R11, R16, R21, R41, R45, R50: 2K7; R_0805_2012Metric
R13, R42: 6K8; R_0805_2012Metric
R14, R15, R20, R43, R44, R48: 47K; R_0805_2012Metric
R18, R47: 3K9; R_0805_2012Metric
R19, R49: 56K; R_0805_2012Metric
R23, R55: 2M2; R_0805_2012Metric
R25, R29, R56: 1K; R_0805_2012Metric
R26: 3K3; R_0805_2012Metric
R27: 2K2; R_0805_2012Metric
R28: 220; R_0805_2012Metric
R33, R57, R58, R59: N/C; R_0805_2012Metric
R53, R54, R66: 4K7; R_0805_2012Metric
R61: 680; R_0805_2012Metric
TP1, TP2: Conn_01x01_Pin; PinHeader_1x01_P2.54mm_Vertical
U1: Pico; RPi_Pico_SMD_TH
U2, U9: 74HC14; SOIC-14_3.9x8.7mm_P1.27mm
U3, U6: 74HC4052D; SO-16_3.9x9.9mm_P1.27mm
U4, U5, U8, U10: LM358; SO-8_3.9x4.9mm_P1.27mm
U7: AMS1117-5.0; SOT-223-3_TabPin2
U11: REF3030; SOT-23
U12: SPX3819M5-L-5-0; SOT-23-5

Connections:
+3V3: D2.2 (K), D4.2 (K), J3.6, J10.7, R53.2, R54.2, U1.36 (3V3), U11.1 (IN)
+5V: C6.1, C8.2, C9.2, C10.2, C16.2, C19.2, C20.2, C21.1, C24.1, R6.2, R7.2, R25.1, R26.2, R28.1, R38.2, R40.2, R56.1, R61.2, U2.14 (VCC), U3.16 (VDD), U4.8 (V+), U5.8 (V+), U6.16 (VDD), U7.2 (VO), U8.8 (V+), U9.14 (VCC), U10.8 (V+), U12.5 (OUT)
+12V: C18.1, C23.1, C25.1, D1.3 (COM), J1.1, J9.1, Q5.2 (S), R4.2, U7.3 (VI), U12.1 (IN), U12.3 (EN)
/ADC1: R58.2, U1.32 (GPIO27_ADC1)
/ADC2: R59.2, U1.34 (GPIO28_ADC2)
/CAS_ERASE: R29.2, U1.16 (GPIO12)
/CAS_MODE: J3.2, U1.29 (GPIO22)
/CAS_PRESENT: J3.7, U1.15 (GPIO11)
/CAS_RD1: Q4.3 (D), R53.1, TP1.1, U1.22 (GPIO17)
/CAS_RD2: Q6.3 (D), R54.1, TP2.1, U1.19 (GPIO14)
/CAS_SOL: D3.2 (K), J3.3, Q5.3 (D)
/CAS_TACHO: J3.5, U1.25 (GPIO19)
/CAS_WR1: U1.21 (GPIO16), U2.11
/CAS_WR2: U1.20 (GPIO15), U9.11
/CAS_WRPROTEC: J3.1, U1.14 (GPIO10)
/CAS_WRSEL1: R62.1, U1.24 (GPIO18)
/CAS_WRSEL2: R63.1, U1.17 (GPIO13)
/EBOOST: J10.1, R66.1, U1.9 (GPIO6)
/LED_ACTIVITY: R60.2, U1.12 (GPIO9)
/LED_READ: R31.2, U1.11 (GPIO8)
/LED_WRITE: R30.2, U1.10 (GPIO7)
/MOTOR: D4.3 (COM), R3.1, U1.27 (GPIO21)
/SOLENOID: D2.3 (COM), R2.1, U1.26 (GPIO20)
/VBUS: Q8.2 (S), R64.2, U1.40 (VBUS)
/VBUSSEQ: C17.1, J6.1, Q8.3 (D)
/VIRTGND: C6.2, C7.1, R12.2, R14.2, R20.2, R22.1, R24.1, R26.1, R27.2, R37.2, R43.2, R48.2, R51.1, R52.1
GND: C7.2, C8.1, C9.1, C10.1, C16.1, C19.1, C20.1, C21.2, C22.1, C24.2, H3.1, J2.2, J5.2, JP2.2 (B), Q3.2 (E), Q4.2 (S), Q6.2 (S), R11.2, R16.2, R21.2, R27.1, R33.2, R41.2, R45.2, R50.2, R57.2, U1.33 (AGND), U2.7 (GND), U3.2 (Y2), U3.4 (Y3), U3.6 (INH), U3.7 (VEE), U3.8 (VSS), U3.9 (B), U3.11 (X3), U3.15 (X2), U4.4 (V-), U5.4 (V-), U6.2 (Y2), U6.4 (Y3), U6.6 (INH), U6.7 (VEE), U6.8 (VSS), U6.9 (B), U6.11 (X3), U6.15 (X2), U7.1 (GND), U8.4 (V-), U9.7 (GND), U10.4 (V-), U11.3 (GND), U12.2 (GND)
GNDD: C18.2, C23.2, C25.2, D2.1 (A), D3.3 (COM), D4.1 (A), D5.1 (K), D6.1 (K), D7.1 (K), D8.1 (K), H1.1, H2.1, H4.1, J3.4, J8.1, J10.2, JP1.1 (A), JP2.1 (A), Q1.2 (S), Q2.2 (S), Q7.2 (E), R1.2, R32.2, U1.3 (GND), U1.8 (GND), U1.13 (GND), U1.18 (GND), U1.23 (GND), U1.28 (GND), U1.38 (GND)
unnamed: C1.1, R10.1, R11.1, U4.1
unnamed: C1.2, R13.2
unnamed: C2.2, C3.1, R15.2, R16.1, R17.2, U4.7
unnamed: C3.2, R17.1, R18.2, R58.1
unnamed: C4.2, C5.1, R19.2, R21.1, U5.1
unnamed: C11.1, R39.1, R41.1, U8.1
unnamed: C11.2, R42.2
unnamed: C12.2, C13.1, R44.2, R45.1, R46.2, U8.7
unnamed: C13.2, R46.1, R47.2, R59.1
unnamed: C14.2, C15.1, R49.2, R50.1, U10.1
unnamed: D1.1 (A), J1.2, Q1.3 (D)
unnamed: D5.2 (A), R30.1
unnamed: D6.2 (A), R31.1
unnamed: D7.2 (A), R60.1
unnamed: D8.2 (A), R61.1
unnamed: J2.1, U3.13 (X)
unnamed: J2.3, U3.3 (Y)
unnamed: J4.1, Q3.3 (C)
unnamed: J4.2, R28.2
unnamed: J5.1, U6.13 (X)
unnamed: J5.3, U6.3 (Y)
unnamed: C17.2, J7.1, JP1.2 (B)
unnamed: J10.3, U1.7 (GPIO5)
unnamed: J10.4, U1.6 (GPIO4)
unnamed: J10.5, U1.5 (GPIO3)
unnamed: J10.6, U1.4 (GPIO2)
unnamed: J10.8, U1.2 (GPIO1)
unnamed: J10.9, U1.1 (GPIO0)
unnamed: Q1.1 (G), R1.1, R3.2
unnamed: Q2.3 (D), Q5.1 (G), R4.1
unnamed: Q2.1 (G), R2.2, R32.1
unnamed: Q3.1 (B), R29.1
unnamed: Q4.1 (G), U2.12
unnamed: Q6.1 (G), U9.12
unnamed: Q7.1 (B), R66.2
unnamed: Q7.3 (C), Q8.1 (G), R64.1
unnamed: R5.1, R6.1, U2.8
unnamed: R23.1, R25.2, R33.1, U2.1, U5.7
unnamed: R36.1, R40.1, U9.8
unnamed: R55.1, R56.2, R57.1, U9.1, U10.7
unnamed: U1.35 (ADC_VREF), U11.2 (OUT)
unnamed: U2.4, U2.5
unnamed: U2.3, U2.9, U2.10
unnamed: U2.2, U2.13
unnamed: R62.2, U3.10 (A)
unnamed: R8.2, U3.12 (X0)
unnamed: R5.2, U3.14 (X1)
unnamed: R9.1, U3.1 (Y0)
unnamed: R7.1, U2.6, U3.5 (Y1)
unnamed: R9.2, R12.1, U4.3 (+)
unnamed: R8.1, R10.2, U4.2 (-)
unnamed: R14.1, U4.5 (+)
unnamed: C2.1, R13.1, R15.1, U4.6 (-)
unnamed: R20.1, U5.3 (+)
unnamed: C4.1, R18.1, R19.1, U5.2 (-)
unnamed: R22.2, R23.2, U5.5 (+)
unnamed: C5.2, R24.2, U5.6 (-)
unnamed: R63.2, U6.10 (A)
unnamed: R34.2, U6.12 (X0)
unnamed: R36.2, U6.14 (X1)
unnamed: R35.1, U6.1 (Y0)
unnamed: R38.1, U6.5 (Y1), U9.6
unnamed: R35.2, R37.1, U8.3 (+)
unnamed: R34.1, R39.2, U8.2 (-)
unnamed: R43.1, U8.5 (+)
unnamed: C12.1, R42.1, R44.1, U8.6 (-)
unnamed: U9.4, U9.5
unnamed: U9.3, U9.9, U9.10
unnamed: U9.2, U9.13
unnamed: R48.1, U10.3 (+)
unnamed: C14.1, R47.1, R49.1, U10.2 (-)
unnamed: R52.2, R55.2, U10.5 (+)
unnamed: C15.2, R51.2, U10.6 (-)
unnamed: C22.2, U12.4 (BP)

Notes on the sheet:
Set to 9.5-9.6V At 12V it can't deliver the current needed for reliable solenoid actuation
*1) R25 to GND changed to +5V
POWER SEQUENCER to avoid inrush current during USB enumeration
ASSUMING MODIFIED TAKEUP REEL SENSOR CAS_TACHO connects to phototransistor's collector
*3) R23 changed to 1M
SX1308 DC-DC可调升压板
#NP-090 originally Changes marked with *#)
*2) 330K changed to 100K probably unimportant

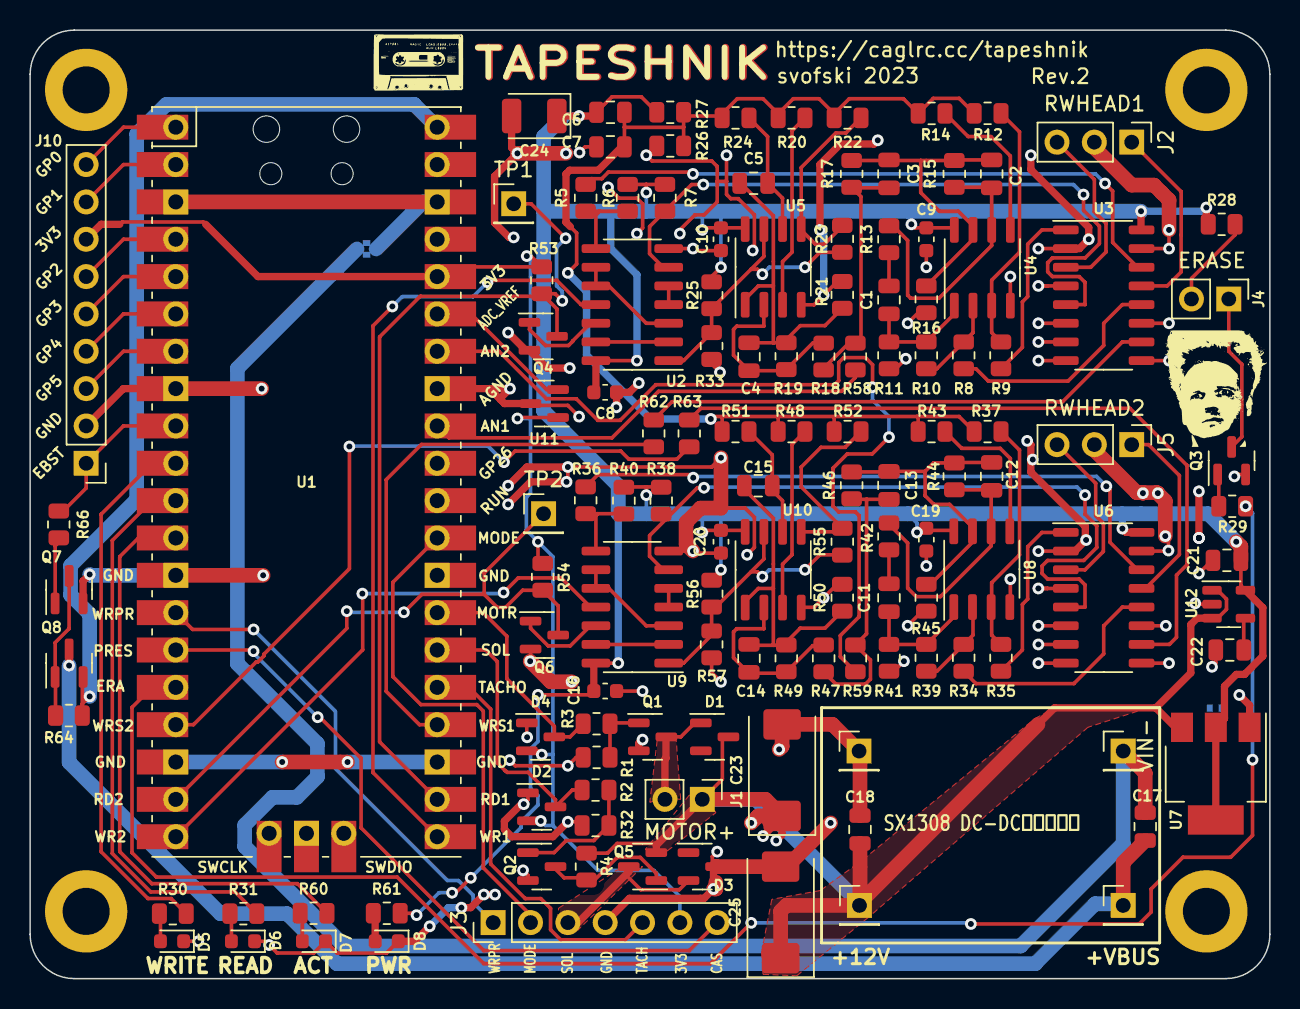
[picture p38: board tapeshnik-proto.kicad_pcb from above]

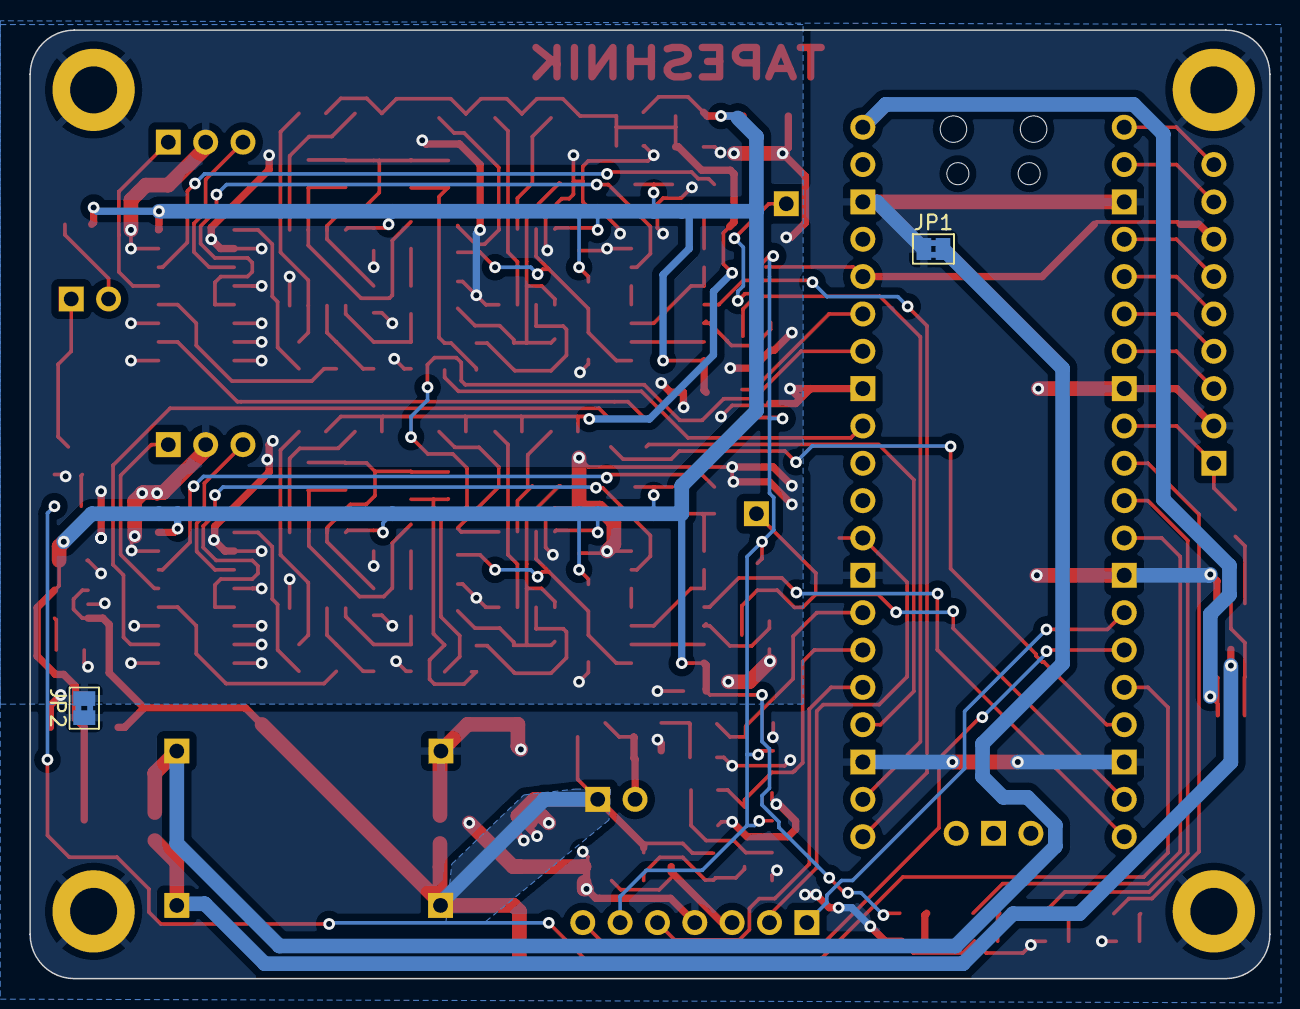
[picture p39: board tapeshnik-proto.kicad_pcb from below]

Board: 2 copper layers, 84.3 x 64.5 mm, 136 parts (2 on the bottom side), 102 nets.

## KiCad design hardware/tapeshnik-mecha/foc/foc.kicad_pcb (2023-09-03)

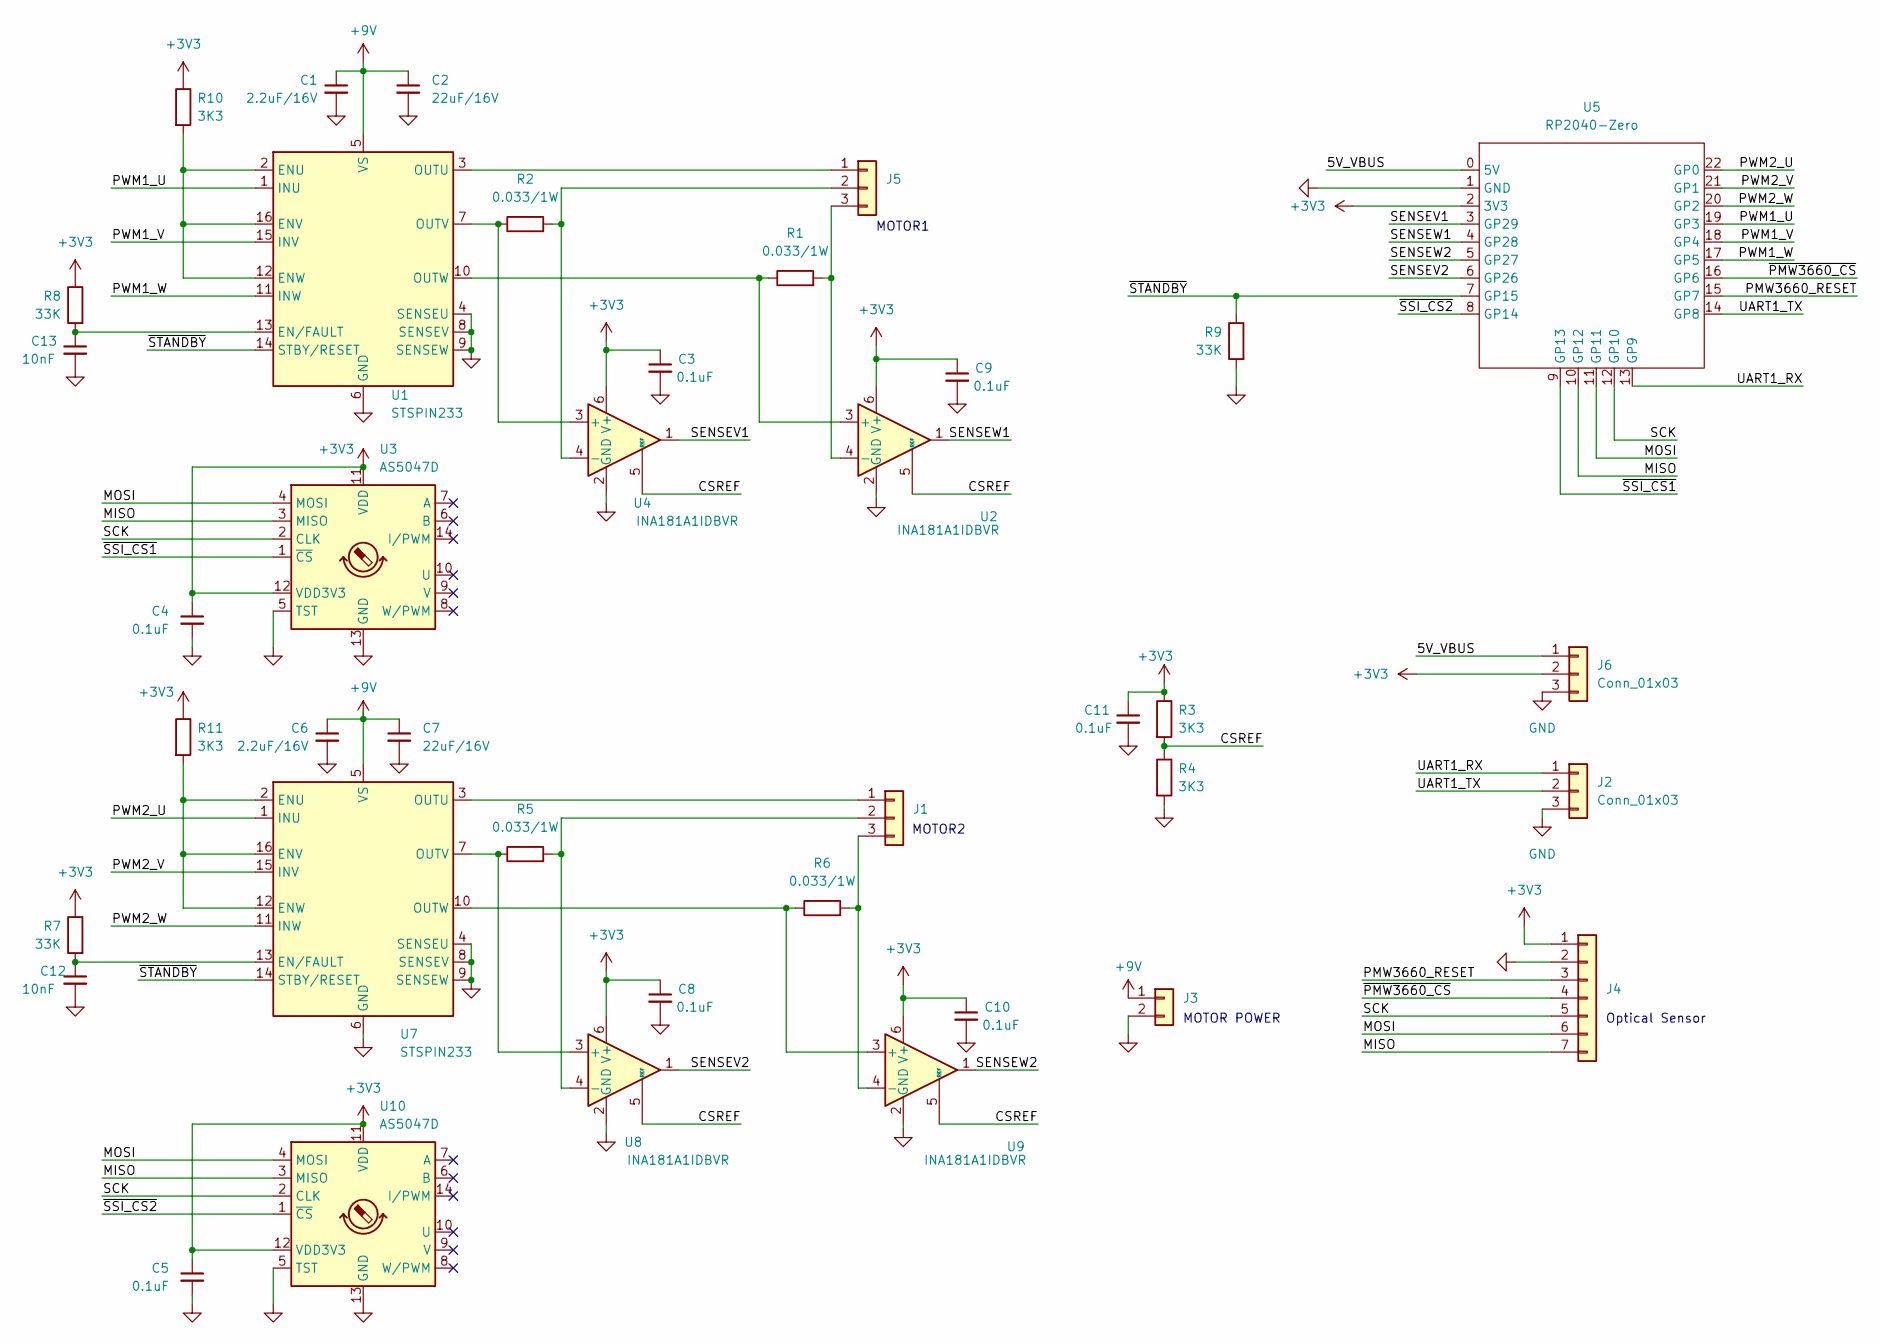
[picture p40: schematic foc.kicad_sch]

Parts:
C1, C6: 2.2uF/16V; C_0603_1608Metric
C2, C7: 22uF/16V; C_0805_2012Metric; LCSC C45783
C3, C4, C5, C8, C9, C10, C11: 0.1uF; C_0402_1005Metric
C12, C13: 10nF; C_0402_1005Metric
J1, J2, J5, J6: Conn_01x03; PinHeader_1x03_P2.54mm_Vertical
J3: Conn_01x02; PinHeader_1x02_P2.54mm_Vertical
J4: Conn_01x07; JST_SH_SM07B-SRSS-TB_1x07-1MP_P1.00mm_Horizontal
R1, R2, R6: 0.033/1W; R_2512_6332Metric; LCSC C2934109
R3, R4: 3K3; R_0603_1608Metric
R5: 0.033/1W; R_2512_6332Metric
R7, R8: 33K; R_0402_1005Metric
R9: 33K; R_0603_1608Metric
R10, R11: 3K3; R_0402_1005Metric
U1, U7: STSPIN233; VQFN-16-1EP_3x3mm_P0.5mm_EP1.8x1.8mm
U2, U4, U8, U9: INA181A1IDBVR; SOT-23-6
U3, U10: AS5047D; TSSOP-14_4.4x5mm_P0.65mm
U5: RP2040-Zero; rp2040-zero

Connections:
+3V3: C3.1, C4.1, C5.1, C8.1, C9.1, C10.1, C11.1, J4.1, J6.2, R3.1, R7.1, R8.1, R10.1, R11.1, U2.6 (V+), U3.11 (VDD), U3.12 (VDD3V3), U4.6 (V+), U5.2 (3V3), U8.6 (V+), U9.6 (V+), U10.11 (VDD), U10.12 (VDD3V3)
+9V: C1.1, C2.1, C6.1, C7.1, J3.1, U1.5 (VS), U7.5 (VS)
/5V_VBUS: J6.1, U5.0 (5V)
/CSREF: R3.2, R4.1, U2.5 (REF), U4.5 (REF), U8.5 (REF), U9.5 (REF)
/MISO: J4.7, U3.3 (MISO), U5.10 (GP12), U10.3 (MISO)
/MOSI: J4.6, U3.4 (MOSI), U5.11 (GP11), U10.4 (MOSI)
/PMW3660_RESET: J4.3, U5.15 (GP7)
/PWM1_U: U1.1 (INU), U5.19 (GP3)
/PWM1_V: U1.15 (INV), U5.18 (GP4)
/PWM1_W: U1.11 (INW), U5.17 (GP5)
/PWM2_U: U5.22 (GP0), U7.1 (INU)
/PWM2_V: U5.21 (GP1), U7.15 (INV)
/PWM2_W: U5.20 (GP2), U7.11 (INW)
/SCK: J4.5, U3.2 (CLK), U5.12 (GP10), U10.2 (CLK)
/SENSEV1: U4.1, U5.3 (GP29)
/SENSEV2: U5.6 (GP26), U8.1
/SENSEW1: U2.1, U5.4 (GP28)
/SENSEW2: U5.5 (GP27), U9.1
/UART1_RX: J2.1, U5.13 (GP9)
/UART1_TX: J2.2, U5.14 (GP8)
/~PMW3660_CS: J4.4, U5.16 (GP6)
/~SSI_CS1: U3.1 (~CS), U5.9 (GP13)
/~SSI_CS2: U5.8 (GP14), U10.1 (~CS)
/~STANDBY: R9.1, U1.14 (STBY/RESET), U5.7 (GP15), U7.14 (STBY/RESET)
GND: C1.2, C2.2, C3.2, C4.2, C5.2, C6.2, C7.2, C8.2, C9.2, C10.2, C11.2, C12.2, C13.2, J2.3, J3.2, J4.2, J6.3, R4.2, R9.2, U1.4 (SENSEU), U1.6 (GND), U1.8 (SENSEV), U1.9 (SENSEW), U1.17 (GND), U2.2 (GND), U3.5 (TST), U3.13 (GND), U4.2 (GND), U5.1 (GND), U7.4 (SENSEU), U7.6 (GND), U7.8 (SENSEV), U7.9 (SENSEW), U7.17 (GND), U8.2 (GND), U9.2 (GND), U10.5 (TST), U10.13 (GND)
unnamed: J1.1, U7.3 (OUTU)
unnamed: J1.2, R5.2, U8.4 (-)
unnamed: J1.3, R6.2, U9.4 (-)
unnamed: J5.1, U1.3 (OUTU)
unnamed: J5.2, R2.2, U4.4 (-)
unnamed: J5.3, R1.2, U2.4 (-)
unnamed: R10.2, U1.2 (ENU), U1.12 (ENW), U1.16 (ENV)
unnamed: C13.1, R8.2, U1.13 (EN/FAULT)
unnamed: R2.1, U1.7 (OUTV), U4.3 (+)
unnamed: R1.1, U1.10 (OUTW), U2.3 (+)
unnamed: R11.2, U7.2 (ENU), U7.12 (ENW), U7.16 (ENV)
unnamed: C12.1, R7.2, U7.13 (EN/FAULT)
unnamed: R5.1, U7.7 (OUTV), U8.3 (+)
unnamed: R6.1, U7.10 (OUTW), U9.3 (+)

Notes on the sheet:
Optical Sensor
MOTOR2
MOTOR1
MOTOR POWER

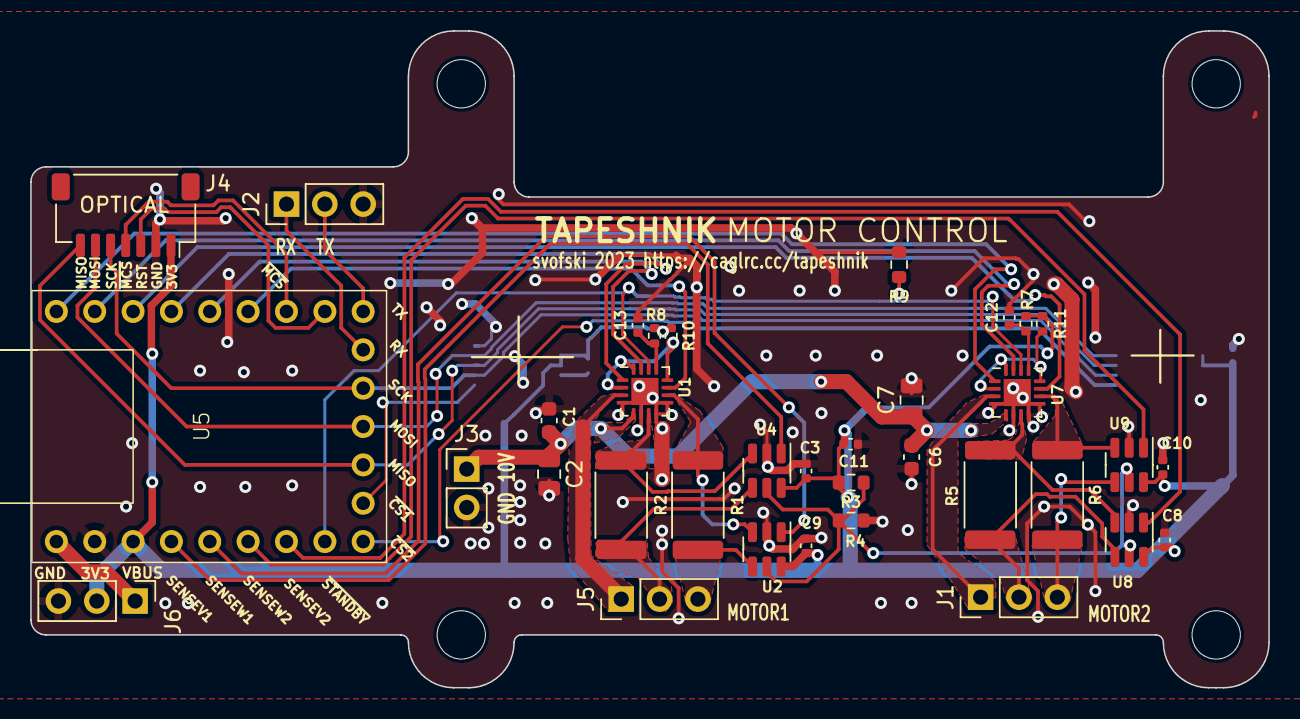
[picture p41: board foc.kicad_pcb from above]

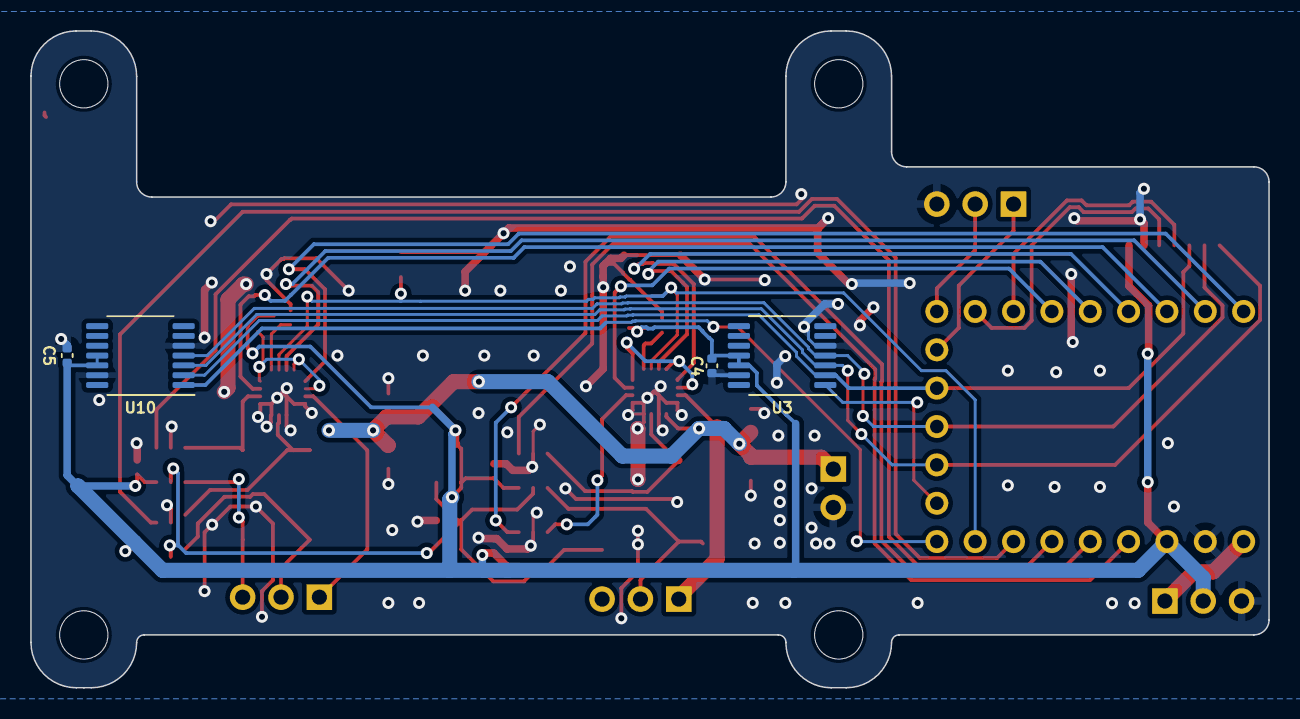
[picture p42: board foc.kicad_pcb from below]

Board: 2 copper layers, 82.0 x 43.5 mm, 39 parts (4 on the bottom side), 39 nets.

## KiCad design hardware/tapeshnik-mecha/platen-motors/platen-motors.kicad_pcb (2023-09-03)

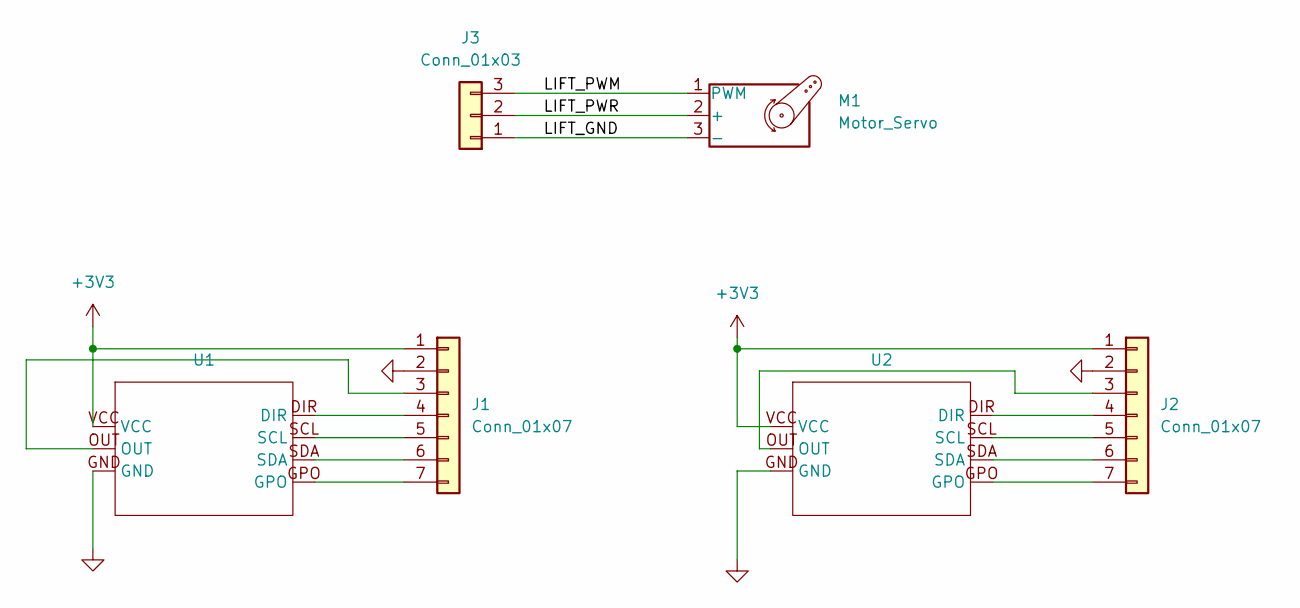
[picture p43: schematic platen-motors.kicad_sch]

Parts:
J1, J2: Conn_01x07; PinHeader_1x07_P2.54mm_Vertical
J3: Conn_01x03; PinHeader_1x03_P2.54mm_Vertical
M1: Motor_Servo; PinHeader_1x03_P2.54mm_Vertical
U1, U2: AS5600-breakout-23x23

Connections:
+3V3: J1.1, J2.1, U1.VCC, U2.VCC
/LIFT_GND: J3.1, M1.3 (-)
/LIFT_PWM: J3.3, M1.1 (PWM)
/LIFT_PWR: J3.2, M1.2 (+)
GND: J1.2, J2.2, U1.GND, U2.GND
unnamed: J1.3, U1.OUT
unnamed: J1.4, U1.DIR
unnamed: J1.5, U1.SCL
unnamed: J1.6, U1.SDA
unnamed: J1.7, U1.GPO
unnamed: J2.3, U2.OUT
unnamed: J2.4, U2.DIR
unnamed: J2.5, U2.SCL
unnamed: J2.6, U2.SDA
unnamed: J2.7, U2.GPO

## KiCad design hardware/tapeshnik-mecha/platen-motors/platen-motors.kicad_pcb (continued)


Board: 2 copper layers, 129.0 x 80.0 mm, 6 parts (0 on the bottom side), 15 nets.

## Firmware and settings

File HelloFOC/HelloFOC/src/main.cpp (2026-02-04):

#include <Arduino.h>
#include <SimpleFOC.h>
#include <encoders/smoothing/SmoothingSensor.h>
#include "PMW3360/PMW3360.h"
#include "deckcontrol.h"
#include "util.h"

#define WITH_MOTORS 1
#define WITH_DECK_CONTROLS 1

void doPlayForward(char *cmd);
void doFastForward(char *cmd);

void doPlayReverse(char *cmd);
void doFastReverse(char *cmd);

void doStop(char *cmd);

void doZeroCounter(char *cmd);

// normal tape rpm 40..100   rpm or 0.6..1.66 rps
// ff tape rpm     400..1000 rpm or 6.7..16.6 rps

constexpr int PIN_TAPE_SENSOR_CS_N = 6;
constexpr int PIN_TAPE_SENSOR_RESET_N = 7;

// motor sensor pins
constexpr int PIN_MOTOR1_SENSOR_CS_N = 13;
constexpr int PIN_MOTOR2_SENSOR_CS_N = 14;

// motor controller pins
constexpr int PIN_STANDBY = 15;

constexpr int HEAD_LIFT_SERVO_PIN = 29;
constexpr int HEAD_LIFT_SERVO_UP = 90;
constexpr int HEAD_LIFT_SERVO_MID = 90;
constexpr int HEAD_LIFT_SERVO_DOWN = 90;

constexpr float speed_max = 40.0;
constexpr float speed_min = -40.0;
constexpr float speed_init = 6.28; // exactly 1 turn/sec
float dspeed = 0;


constexpr float TAPE_PLAY_SPEED = 3.14;
constexpr float TAPE_FAST_SPEED = 6.28 * 4;
constexpr float TAPE_FAST_SPEED_REW = 6.28 * 4;

int tape_counter = 0;
int tape_sensor_squal = 0;

// BLDC motor instance: 
// DC-2813C http://www.jdpowersky.com/en/p-info.aspx?cid=1&id=116
// DC-2813C is 12N14P, 12 slots, 14 poles
// 11.3 ohm

// MOTOR1 (supply spindle)
BLDCMotor motor1 = BLDCMotor(/*pp=*/7, /*R=*/11.3, /*KV=*/ 196); 
BLDCDriver3PWM driver1 = BLDCDriver3PWM(3, 4, 5); // PWM1_U/V/W, no enable
MagneticSensorSPI magneticSensor1 = MagneticSensorSPI(AS5047_SPI, PIN_MOTOR1_SENSOR_CS_N);
SmoothingSensor smoothingSensor1 = SmoothingSensor(magneticSensor1, motor1);

// MOTOR2 (takeup spindle)
BLDCMotor motor2 = BLDCMotor(/*pp=*/7, /*R=*/11.3, /*KV=*/ 196); 
BLDCDriver3PWM driver2 = BLDCDriver3PWM(0, 1, 2); // PWM1_U/V/W, no enable
MagneticSensorSPI magneticSensor2 = MagneticSensorSPI(AS5047_SPI, PIN_MOTOR2_SENSOR_CS_N);
SmoothingSensor smoothingSensor2 = SmoothingSensor(magneticSensor2, motor2);

// somehow changing SPI (SPI0) parameters seems to kill everything, not sure what's going on
//                        rx, cs,    sck,tx
SPIClassRP2040 SPIn(spi1, 12, NOPIN, 10, 11); // need be valid pins for same SPI channel, else fails blinking 4 long 4 short

// head lift servo
Servo head_lift_servo;

// instantiate the commander
Commander command = Commander(Serial);
void doMotor1(char* cmd) { command.motor(&motor1, cmd); }
void doMotor2(char* cmd) { command.motor(&motor2, cmd); }
void doHeadLift(char *cmd) {
  int us = atoi(&cmd[0]);
  Serial.printf("Head lift: %d us\n", us);
  //if (us < 1000 || us > 2000) {
  //  Serial.printf("Head lift: arg is microseconds must be in range [1000..2000] (got %d)\n", us);
  //  return;
  //}
  head_lift_servo.writeMicroseconds(us);
}

const char * fail = 0;

PMW3360 tape_sensor;

DeckControl deckControl(&motor1, &motor2, &head_lift_servo);

void pidSetup(BLDCMotor& motor)
{

  #if 1 
  // velocity loop PID
  motor.PID_velocity.P = 0.1;
  motor.PID_velocity.I = 1;//0.025; // maybe 1 is too heavy?
  motor.PID_velocity.D = 0.0;
  motor.PID_velocity.output_ramp = 8000.0;
  motor.PID_velocity.limit = 2.0;//20.0;

//  // Low pass filtering time constant
  motor.LPF_velocity.Tf = 0.01f;    // larger value -> bigger start/stop jerk
  #endif
  #if 0
  motor.PID_velocity.P = 0.2;
  motor.PID_velocity.I = 0.025;
  motor.PID_velocity.D = 0.0;
  motor.PID_velocity.output_ramp = 50.0;
  motor.PID_velocity.limit = 1.0;

  motor.LPF_velocity.Tf = 0.3f;    // larger value -> bigger start/stop jerk
  #endif

  // angle loop PID
  motor.P_angle.P = 30.0;
  motor.P_angle.I = 0.0;
  motor.P_angle.D = 5.0;
  motor.P_angle.output_ramp = 100.0;
  motor.P_angle.limit = 20.0;

  // pwm modulation settings
  motor.foc_modulation = FOCModulationType::SpaceVectorPWM;
  motor.modulation_centered = 1.0f;

  // with sx1308 there seems to be not enough power
  // 4.0 is the max safe value, 4.2 is mostly ok but no
  // 
  //motor.voltage_limit = 4.0f;

  // for external 9V
  motor.voltage_limit = 6.0f;
}

void sensorInit(MagneticSensorSPI &sensor)
{
  sensor.clock_speed = 10'000'000;
  sensor.init(&SPIn);
}

void motorInit(BLDCMotor &motor, BLDCDriver3PWM &driver, Sensor &sensor, uint8_t pin_standby)
{
  // initialise magnetic sensor hardware
  motor.linkSensor(&sensor);
  
  // driver config
  driver.voltage_power_supply = 9; // Replace with your power supply voltage
  driver.pwm_frequency = 24000; // default 24000
  driver.init();
  motor.linkDriver(&driver);
  motor.voltage_sensor_align = 2;

  motor.torque_controller = TorqueControlType::voltage;
  //motor.controller = MotionControlType::torque;
  //motor.target = 0.2; // Volts 

  //motor.controller = MotionControlType::velocity;
  motor.controller = MotionControlType::torque;
  motor.target = 0; // radians/sec 

  pidSetup(motor);

  //motor.useMonitoring(Serial); 

  // set the target velocity (rad/s)
  //motor.target = 6.28; // Example: 5 radians per second

  
  // init motor
  if (!motor.init()) {
    fail = "motor init failed!";
    return;
  }

  motor.motion_downsample = 3;
  
  // initFOC needs motor to actually work
  // enable motori
  pinMode(pin_standby, OUTPUT);
  digitalWrite(pin_standby, HIGH);

  //digitalWrite(PIN_STANDBY, LOW);

  // align sensor and start FOC
  if(!motor.initFOC()){
    fail = "FOC init failed!";
    return;
  }

  Serial.printf("monitorInit: motion_downsample=%d\n", motor.motion_downsample);
} 

void sensor_dumbtest(MagneticSensorSPI &sensor1, MagneticSensorSPI &sensor2)
{
  sensor1.clock_speed = 10'000'000;
  sensor1.init(&SPIn);
  sensor2.clock_speed = 10'000'000;
  sensor2.init(&SPIn);
  for (;;) {
    sensor1.update();
    sensor2.update();
    Serial.print(sensor1.getAngle());
    Serial.print(" ");
    Serial.println(sensor2.getAngle());
  }
}

void motorLoop(BLDCMotor &motor)
{
  motor.loopFOC();
  motor.move();
}

void tape_sensor_setup()
{
  pinMode(PIN_TAPE_SENSOR_RESET_N, OUTPUT);
  digitalWrite(PIN_TAPE_SENSOR_RESET_N, LOW);
  _delay(2);
  digitalWrite(PIN_TAPE_SENSOR_RESET_N, HIGH);
  _delay(100);
  bool succ;
  do {
    succ = tape_sensor.begin(&SPIn, PIN_TAPE_SENSOR_CS_N);
    Serial.print("PMW3360 init ok: "); Serial.println(succ);
    _delay(1000);
  } while(!succ);
}

void tape_sensor_poll()
{
  PMW3360_DATA data = tape_sensor.readBurst();
  
  if(data.isOnSurface && data.isMotion)
  {
    //Serial.print(data.dx);
    //Serial.print("\t");
    //Serial.print(data.dy);
    //Serial.println();
    deckControl.optical_input(data.dy, data.SQUAL);

    tape_counter += data.dy;
    tape_sensor_squal = data.SQUAL;
    //if (data.SQUAL < 20) {
    //  Serial.print("SQUAL LOW! "); Serial.println(data.SQUAL);
    //}
  }
  else {
    //Serial.print("pmw3360 isOnSurface="); Serial.print(data.isOnSurface);
    //Serial.print("pmw3360 isMotion="); Serial.println(data.isMotion);
  }
}


void setup() {
  //_delay(1000);
  Serial.begin(115200);

  pinMode(PIN_MOTOR1_SENSOR_CS_N, OUTPUT);
  digitalWrite(PIN_MOTOR1_SENSOR_CS_N, HIGH);
  pinMode(PIN_MOTOR2_SENSOR_CS_N, OUTPUT);
  digitalWrite(PIN_MOTOR2_SENSOR_CS_N, HIGH);

  head_lift_servo.attach(HEAD_LIFT_SERVO_PIN);
  head_lift_servo.write(HEAD_LIFT_SERVO_UP);

#if WITH_MOTORS
  //_delay(2000);
  //_delay(250);
  SimpleFOCDebug::enable(&Serial);
  Serial.println("simpleFOC setup begins");

  //motor1.useMonitoring(Serial); 
  sensorInit(magneticSensor1);
  motorInit(motor1, driver1, smoothingSensor1, PIN_STANDBY);

  // pull the slack on supply reel after initialisation
  motor1.controller = MotionControlType::torque;
  motor1.target = 0.02; // Volts 
  for (int i = 0; i < 50; ++i) {
    motorLoop(motor1);
    _delay(1);
  }

  //motor2.useMonitoring(Serial); 
  sensorInit(magneticSensor2);
  motorInit(motor2, driver2, smoothingSensor2, PIN_STANDBY);

  motor1.target = 0;
  motor2.target = 0;

  // head lift calibration
  command.add('H', doHeadLift, "Head lift");

  // add target command M
  command.add('M', doMotor1, "Motor 1");
  command.add('N', doMotor2, "Motor 2");

#if WITH_DECK_CONTROLS
  command.add('f', doPlayForward, "PLAY.F");
  command.add('F', doFastForward, "FAST.F");
  command.add('r', doPlayReverse, "PLAY.R");
  command.add('R', doFastReverse, "FAST.R");

  command.add('S', doStop, "STOP");
  command.add('s', doStop, "STOP");
  
  command.add('0', doZeroCounter, "ZERO");
#endif

  Serial.println(F("Motor ready."));
  Serial.println(F("Set the target using serial terminal and command M:"));
#endif
  _delay(1000);
  Serial.println("Initialising PMW3360");
  tape_sensor_setup();
}

enum state { 
  S_DEFAULT,
  S_STOP,
  S_STOP1,
  S_STOP2,
  S_STOP3,
  S_PLAY,
  S_PLAY_FF1,
  S_PLAY1,
  S_PLAY2,
  S_FF,
  S_FF1,
  S_FF2,
  S_REW,
  S_REW1,
  S_REW2
  };

int tape_state = S_DEFAULT;
int tape_state_req = S_DEFAULT;
int tape_state_next = -1;
unsigned long tape_state_timer = 0;

BLDCMotor *stopmotor1, *stopmotor2;

void control_fsm()
{
  switch (tape_state) {
    case S_DEFAULT:
    case S_PLAY:
    case S_FF:
    case S_REW:
      if (tape_state_req == S_STOP) {
        if (tape_state != S_DEFAULT && !(tape_state >= S_STOP1 && tape_state <= S_STOP3)) {
          if (motor2.controller == MotionControlType::velocity) {
            stopmotor1 = &motor1;
            stopmotor2 = &motor2;
          }
          else {
            stopmotor1 = &motor2;
            stopmotor2 = &motor1;
          }
          tape_state = S_STOP1;
        }
      }
      else if (tape_state_req == S_PLAY) {
        if (tape_state == S_FF) {
          Serial.println("quick FF->PLAY_FF1");
          tape_state = S_PLAY_FF1; // no need to apply pretension from FF
        }
        else if (!(tape_state >= S_PLAY1 && tape_state <= S_PLAY2)) {
          tape_state = S_PLAY1;
        }
      }
      else if (tape_state_req == S_FF) {
        if (tape_state == S_REW) {
          tape_state = S_STOP1;
          tape_state_next = S_FF1;
        }
        else if (!(tape_state >= S_FF1 && tape_state <= S_FF2)) {
          tape_state = S_FF1;
        }
      }
      else if (tape_state_req == S_REW) {
        if (tape_state == S_FF) {
          tape_state = S_STOP1;
          tape_state_next = S_REW1;
        }
        if (!(tape_state >= S_REW1 && tape_state <= S_REW2)) {
          tape_state = S_REW1;
        }
      }
      tape_state_req = S_DEFAULT;
      break;

    case S_STOP1:
      if (motor2.controller == MotionControlType::velocity) {
        if (fabs(motor2.shaft_velocity) > 3.14f) {
          motor2.target = fsgn(motor2.target) * (fabs(motor2.target) - 0.1f);
        }
        else {
          tape_state = S_STOP2;
        }
      }
      else if (motor1.controller == MotionControlType::velocity) {
        if (fabs(motor1.shaft_velocity) > 3.14f) {
          motor1.target = fsgn(motor1.target) * (fabs(motor1.target) - 0.1f);
        }
        else {
          tape_state = S_STOP2;
        }
      }
      else {
        tape_state = S_STOP2;
      }
      tape_state_timer = millis() + 25;
      break;
    case S_STOP2:
      if (millis() > tape_state_timer) {
        // revert motor swap before applying torque
        motor1.controller = MotionControlType::torque;
        motor1.target = 0.025;

        motor2.controller = MotionControlType::torque;
        motor2.target = -0.025;

        tape_state_timer = millis() + 50;
        tape_state = S_STOP3;
        Serial.println("->S_STOP3");
      }
      break;
    case S_STOP3:
      if (millis() > tape_state_timer) {
        stopmotor1->target = 0;
        stopmotor2->target = 0;
        tape_state = S_DEFAULT;
        if (tape_state_next >= 0) {
          tape_state = tape_state_next;
          tape_state_next = -1;
        }
        Serial.print("STOP->"); Serial.println(tape_state);
      }
      break;
    case S_PLAY1:
      // pull the slack on supply reel after initialisation
      motor1.controller = MotionControlType::torque;
      motor1.target = 0.02; 
      motor2.controller = MotionControlType::torque;
      motor2.target = -0.02; 
      tape_state_timer = millis() + 30;
      tape_state = S_PLAY2;
      break;
    case S_PLAY2:
      if (millis() > tape_state_timer) {
        motor1.controller = MotionControlType::torque;
        motor1.target = 0.02; 

        motor2.controller = MotionControlType::velocity;
        motor2.target = -TAPE_PLAY_SPEED; // 1 rps
        tape_state = S_PLAY;
      }
      break;
    case S_PLAY_FF1:
      if (motor2.target < -TAPE_PLAY_SPEED) {
        motor2.target += 0.01;
      }
      else {
        tape_state = S_PLAY2;
      }
      break;
    case S_FF1:
      // pull the slack on supply reel after initialisation
      motor1.controller = MotionControlType::torque;
      motor1.target = 0.02; // Volts
      motor2.controller = MotionControlType::velocity;
      motor2.target = -TAPE_PLAY_SPEED;
      tape_state_timer = millis() + 250;
      tape_state = S_FF2;
      break;
    case S_FF2:
      if (millis() > tape_state_timer) {
        motor2.controller = MotionControlType::velocity;
        motor2.target = -TAPE_FAST_SPEED;
        tape_state = S_FF;
      }
      break;
    case S_REW1:
      motor1.controller = MotionControlType::velocity;
      motor1.target = TAPE_PLAY_SPEED;
      motor2.controller = MotionControlType::torque;
      motor2.target = -0.02;
      tape_state_timer = millis() + 250;
      tape_state = S_REW2;
      break;
    case S_REW2:
      if (millis() > tape_state_timer) {
        Serial.println("->S_REW");
        motor1.target = TAPE_FAST_SPEED_REW;
        tape_state = S_REW;
      }
      break;
  }
}

void doPlayForward(char *cmd) {
    deckControl.press_button(DeckButton::PLAY_FORWARD);
}

void doFastForward(char *cmd) {
    deckControl.press_button(DeckButton::FAST_FORWARD);
}

void doPlayReverse(char *cmd) {
    deckControl.press_button(DeckButton::PLAY_REVERSE);
}

void doFastReverse(char *cmd) {
    deckControl.press_button(DeckButton::FAST_REVERSE);
}

void doStop(char *cmd) {
    deckControl.press_button(DeckButton::STOP);
}

void doZeroCounter(char *cmd) {
  tape_counter = 0;
}

unsigned long tape_counter_print_time = millis();
unsigned long tape_sensor_poll_time = millis();
unsigned long poll_interval = 0;
unsigned long last_poll_us = 0;


void loop() {
#if WITH_MOTORS
  motorLoop(motor1);
  motorLoop(motor2);

  //motor1.monitor();
  command.run();

#endif
#if WITH_DECK_CONTROLS
  //control_fsm();
  tape_sensor_poll();
  deckControl.loop();
#endif


  //uint64_t new_micros = micros();
  //poll_interval = (poll_interval + (new_micros - last_poll_us)) >> 1;
  //last_poll_us = micros();

  //if (millis() - tape_counter_print_time > 250) {
  //  tape_counter_print_time = millis();
  //  Serial.print(" M1 w: "); Serial.print(motor1.shaft_velocity); Serial.print(" A:"); Serial.print(motor1.shaft_angle);
  //  Serial.print(" M2 w: "); Serial.print(motor2.shaft_velocity); Serial.print(" A:"); Serial.print(motor2.shaft_angle);

  //  Serial.print(" POS:"); Serial.print(tape_counter);
  //  Serial.print(" poll_us:"); Serial.print(poll_interval);
  //  Serial.print(" SQUAL: "); Serial.println(tape_sensor_squal);
  //}
}

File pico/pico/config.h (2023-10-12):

#pragma once

/* time in milliseconds before motor turns off after STOP */
#define MOTOR_OFF_DELAY 1500


#define GPIO_EBOOST 6 // 1 = enable 12V boost converter

//     ___ 
// ___/ 0 \_____
#define GPIO_MODE_ENTRY 22
#define GPIO_MOTOR_CONTROL 21
#define GPIO_SOLENOID_CONTROL 20

#define GPIO_WRHEAD 16  // pi pico pin 21, green wire
#define GPIO_RDHEAD 17  // pi pico pin 22, yellow wire
#define GPIO_WREN   18  // 1 = write, 0 = read

#define GPIO_TACHO 19

#define MOD_HALFPERIOD  8     // number of clocks per half-period in modulation
                              // also hardcoded in bitstream.pio !
#define MOD_FREQ        7000  // max bit flipping frequency
                              // mfm: 9600 almost works but has trouble syncing
                              //      3300 is rock solid
                              //      6600 seems solid
                              //      7000 is solid with A1 sync
                              //      8000 feels good until it isn't
                              // fm:  6600 ok
                              // debugbuf raw-to-samplerate = MOD_FREQ*4
#define SOLENOID_PULSE_MS 25

#define GPIO_READ_LED   8
#define GPIO_WRITE_LED  7
#define GPIO_ACT_LED    9

#define BOT_LEADER_LEN      256
#define SECTOR_LEADER_LEN   8
#define DATA_LEADER_LEN     8
#define SECTOR_TRAILER_LEN  8

#define CODEC_MFM 1

#ifdef CODEC_MFM
#define modulate    mfm_encode_twobyte
#define demodulate  mfm_decode_twobyte
#endif

#ifdef CODEC_FM
#define modulate    fm_encode_twobyte
#define demodulate  fm_decode_twobyte
#endif

// not modulated, these words are written bit by bit
#ifdef CODEC_FM
constexpr uint32_t LEADER = 0xAAAAAAAA;
constexpr uint32_t SYNC   = 0xAAA1A1A1;
#endif

#ifdef CODEC_MFM
constexpr uint32_t LEADER       = 0xCCCCCCCC;
constexpr uint32_t SYNC_SECTOR  = 0xCCCCCCC7;
constexpr uint32_t SYNC_DATA    = 0xCCCCCCE3;
#endif

#define SECTOR_NUM_REPEATS  4

// number of subblocks in sector
constexpr uint32_t FEC_BLOCKS_PER_SECTOR = 4;

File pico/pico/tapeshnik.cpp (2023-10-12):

/**
 * Copyright (c) 2023 svofski
 */

#include <stdio.h>
#include "pico/stdlib.h"
#include "hardware/gpio.h"
#include "hardware/pwm.h"

#include "config.h"

#include "debounce.h"
#include "wheel.h"
#include "mainloop.h"
#include "tacho.h"
#include "bitstream.h"
#include "util.h"

#define ML_NO_REQUEST   0
#define ML_STOP_REQUEST ' '
volatile int mainloop_request = ML_NO_REQUEST;

Boost boost(GPIO_EBOOST);
Motor motor(boost, GPIO_MOTOR_CONTROL);
Solenoid solenoid(GPIO_SOLENOID_CONTROL);
Wheel wheel(motor, solenoid, GPIO_MODE_ENTRY);
Bitstream bstream(wheel, GPIO_RDHEAD, GPIO_WRHEAD, GPIO_WREN, GPIO_READ_LED,
        GPIO_WRITE_LED);

void request_wheel_stop()
{
    mainloop_request = ML_STOP_REQUEST;
}

char tacho_counter_str[16];
int last_tacho_counter = -1;
int last_wheel_position = -1;
int last_motor_status = -1;

int slice_num;

void freq_sweep()
{
    gpio_set_function(GPIO_WRHEAD, GPIO_FUNC_PWM);
    slice_num = pwm_gpio_to_slice_num(GPIO_WRHEAD);   // GP16, pin 21
    pwm_set_clkdiv_int_frac(slice_num, 62, 8);   // pwm slice frequency 125MHz/62.5 = 2MHz
    // useful sweep range: 100Hz..20000Hz
    // wrap = [2e6/100..2e6/20000] = [20000..100]
    pwm_set_enabled(slice_num, true);
    
    printf("linear sweep %d..%d Hz... on pin 21 ", 2000000/20000, 2000000/100);
    for (int i = 20000; i >= 100; --i) {
        pwm_set_wrap(slice_num, i);
        pwm_set_chan_level(slice_num, PWM_CHAN_A, i >> 1);
        sleep_ms(2);
    }
    pwm_set_enabled(slice_num, false);
    printf("done\n");
}

void freq_8(int hz)
{
    gpio_set_function(GPIO_WRHEAD, GPIO_FUNC_PWM);
    auto slice_num = pwm_gpio_to_slice_num(GPIO_WRHEAD);   // GP16, pin 21
    pwm_set_clkdiv_int_frac(slice_num, 62, 8);   // pwm slice frequency 125MHz/62.5 = 2MHz
    // useful sweep range: 100Hz..20000Hz
    // wrap = [2e6/100..2e6/20000] = [20000..100]
    pwm_set_enabled(slice_num, true);
    
    printf("20sec of %d Hz... on pin 21 ", hz);
    int div = static_cast<int>(125000000/62.5/hz);
    pwm_set_wrap(slice_num, div);
    pwm_set_chan_level(slice_num, PWM_CHAN_A, div >> 1);
    //sleep_ms(20000);
    //pwm_set_enabled(slice_num, false);
    //gpio_set_function(GPIO_WRHEAD, GPIO_FUNC_NULL);
    //printf("done\n");
}

void freq_stop()
{
    pwm_set_enabled(slice_num, false);
    gpio_set_function(GPIO_WRHEAD, GPIO_FUNC_NULL);
}

int main() {
    stdio_init_all();

    printf("tapeshnik\n");

    debounce_init();
    //wheel_init(GPIO_MOTOR_CONTROL, GPIO_SOLENOID_CONTROL, GPIO_MODE_ENTRY);

    tacho_init(GPIO_TACHO);

    wheel.init();

    //gpio_disable_pulls(GPIO_RDHEAD);
    //gpio_pull_up(GPIO_RDHEAD);
    //gpio_set_dir(GPIO_RDHEAD, /* out */ true);
    //gpio_put(GPIO_RDHEAD, 1);

    // Wait forever
    while (1) {
        int c = mainloop_request;
        mainloop_request = ML_NO_REQUEST;
        if (c == ML_NO_REQUEST) {
            c = getchar_timeout_us(100);
            if (mainloop_request != ML_NO_REQUEST) {
                c = mainloop_request;
            }
        }
        switch (c) {
            case 'z': solenoid.pulse_ms(50);
                      break;
            case 'm': motor.enable(!motor.get_status());
                      printf("motor=%d\n", motor.get_status());
                      break;
            case ' ': wheel.stop();
                      freq_stop();
                      break;
            case 'p': wheel.play();
                      break;
            case 'f': wheel.ff();
                      break;
            case 'r': wheel.rew();
                      break;
            case '0': tacho_set_counter(0);
                      break;
            case 's': freq_sweep();
                      break;
            case '4': freq_8(4000);
                      break;
            case '8': freq_8(8000);
                      break;
            case '1': freq_8(10000);
                      break;
            case '2': freq_8(20000);
                      break;
            case '3': freq_8(30000);
                      break;
            //case '5': bstream.test();
            //          break;
            //case 'w': bstream.test(BS_TX);
            //          break;
            //case 'l': bstream.test(BS_RX);
            //          break;
            //case 'e': bstream.test_sector_rewrite();
            //          break;
            case 'F': bstream.llformat();
                      break;
            case 'l': bstream.sector_scan(65535);
                      break;
            case 'w': bstream.test_write();
                      break;
            case 10:
            case 13:
                      info_println("\nHelp: m=motor, p=play, f=ff, r=rew, space=stop, 0=zero counter");
                      break;
        }

        if (tacho_get_counter() != last_tacho_counter
                || wheel.get_position() != last_wheel_position
                || motor.get_status() != last_motor_status) {
            last_tacho_counter = tacho_get_counter();
            last_wheel_position = wheel.get_position();
            last_motor_status = motor.get_status();
            snprintf(tacho_counter_str, 16, "  %+05d    \r", last_tacho_counter);
            
            int bgcolor = last_motor_status ? 44 : 42;
            switch (last_wheel_position) {
                case WP_STOP:
                    blink_off();
                    print_color(bgcolor, 37, "   STOP  ", tacho_counter_str);
                    break;
                case WP_PLAY:
                    blink_on();
                    print_color(bgcolor, 37, " <|PLAY  ", tacho_counter_str);
                    break;
                case WP_FF:
                    blink_on();
                    print_color(bgcolor, 37, "  <<FF   ", tacho_counter_str);
                    break;
                case WP_REW:
                    blink_on();
                    print_color(bgcolor, 37, "  REW>>  ", tacho_counter_str);
                    break;
            }
        }
    };

    return 0;
}

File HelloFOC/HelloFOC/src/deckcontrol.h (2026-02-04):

#pragma once

#define USE_VELOCITY_CONTROL 1

#include <Arduino.h>
#include <SimpleFOC.h>
#include <Servo.h>
#include "util.h"

struct MotorInfo {
    BLDCMotor *motor;

    float zero_shaft_angle;   // after rewind
    float last_shaft_angle;   // last measurement
    float w;                  // measured angular velocity rad/s
    float w_average;
    float numturns;           // number of turns after rewind
    
    float total_numturns;     // calibrated value
};

enum class DeckDirection {
    FORWARD,
    REVERSE
};

enum class DeckState {
    STOP,
    STOP_RAMPDOWN, // slowing down
    STOP_TENSION,
    PLAY,
    PLAY_RAMPUP, // speeding up
};

enum class SetSpeedOption {
    NONE,
    AUTOSTOP
};

enum class DeckButton {
    NO_BUTTON,
    STOP,
    PLAY_FORWARD,
    PLAY_REVERSE,
    FAST_FORWARD,
    FAST_REVERSE
};

enum class HeadPosition {
    UP,
    MID,
    DOWN
};

class DeckControl {
private:
    BLDCMotor *motor1;
    BLDCMotor *motor2;

    MotorInfo mi1;
    MotorInfo mi2;

    MotorInfo *supply;
    MotorInfo *takeup;

    float tape_speed_sp;     // speed setpoint (sign == direction)
    float tape_velocity;

    uint64_t last_measure_micros;

    Servo *head_lift_servo;


public:
    static constexpr float OVER_2PI = 1.0f / M_TWOPI;
    //static constexpr uint32_t W_INTERVAL_US = 1'000'000; // 1s for scale w in rad/s
    //static constexpr float W_SCALE = 1.0f;  // or e.g. interval=100'000, scale=10.f
    static constexpr uint32_t W_INTERVAL_US = 1'000'000 / 8; // measure 8 times per second
    static constexpr float W_SCALE = 8.0f;  // scale to rad/s

    #if USE_VELOCITY_CONTROL
    static constexpr float TORQUE_SUPPLY = 0.03f;
    #else
    static constexpr float TORQUE_SUPPLY = 0.03f;
    #endif
    static constexpr float TORQUE_BRAKE = 0.08f;

    static constexpr float TORQUE_TAKEUP_NORMAL = 0.2f;
    static constexpr float TORQUE_TAKEUP_FAST = 0.3f;

    static constexpr float NORMAL_SPEED = 47.7e-3f;
    static constexpr float FF_SPEED = 30 * 47.7e-3f;
    // empty reel radius = 11.5mm (TASCAM cassette, approx)
    static constexpr float R0 = 11.5e-3f;
    static constexpr float MIN_W = 0.01f; // if spindle doesn't go at least this fast, autostop
    float tape_thickness = 13e-6; // 13um

    int print_update_ctr = 0;
    static constexpr int PRINT_UPDATE_INTERVAL = 128; // skip 8 measurements between printing debug info

    DeckState state = DeckState::STOP;
    DeckDirection direction;
    int autostop_count;
    bool autostopping;
    static constexpr int AUTOSTOP_LOCKED_THRESHOLD = 1; // autostop if spindles don't spin
    static constexpr int AUTOSTOP_FREESPIN_THRESHOLD = 40; // autostop if seem to spin freely

    int stopping_cycles_ctr; // (update cycles) tension the tape before relaxing motors
    static constexpr int STOPPING_CYCLES = 40; // intervals in VELOCITY_RAMP_MS

    DeckButton next_action = DeckButton::NO_BUTTON;

    // servo positions in microseconds
    static constexpr int HEAD_SERVO_UP_POS = 1750;
    static constexpr int HEAD_SERVO_MID_POS = 1600;
    static constexpr int HEAD_SERVO_DOWN_POS = 1400;

    float tape_counter;
    int optical_counter;
    float optical_squal;

public:
    DeckControl() = delete;
    DeckControl(DeckControl&) = delete;
    DeckControl(DeckControl&&) = delete;
    DeckControl(BLDCMotor *m1, BLDCMotor *m2, Servo *head_lift_servo)
    {
        mi1.motor = m1;
        mi2.motor = m2;

        supply = &mi1;
        takeup = &mi2;
        direction = DeckDirection::FORWARD;
        state = DeckState::STOP;
        set_zero();

        // default calibration
        mi2.total_numturns = 818;
        mi1.total_numturns = 818;
        tape_thickness = 13e-6; // 13um

        this->head_lift_servo = head_lift_servo;
    }

    void calibrate()
    {
        if (direction != DeckDirection::FORWARD) {
            Serial.println("calibrate: not forward EOT");
            return;
        }
        
        mi1.total_numturns = mi2.total_numturns = mi2.numturns;
        // R0 + delta = total roll thickness
        float delta = (mi1.w_average / mi2.w_average - 1) * R0;
        tape_thickness = delta / mi1.total_numturns;
        Serial.printf("calibrate: numturns=%f delta=%f tape_thickness=%f\n",
                mi1.total_numturns, delta, tape_thickness);
    }

    bool stopped() const 
    {
        return state == DeckState::STOP;
    }
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

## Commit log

2023-07-02 detect too fast spin in play mode
    [tacho.c]
2023-07-22 updated the head amplifiers circuit
2023-07-22 kicad files
    [tapeshnik-proto.kicad_pcb, tapeshnik-proto.kicad_sch]
2023-08-05 mfm send-receive on a loopback wire
    wire between gpio 16 and 17
    super-naiive rx tolerates slightly faster send, but not slower
2023-08-05 dll tracking of mfm with pid, etc
    more artificial tests before i'm ready for running it on tape. dll
    tracker shows slightly better performance than fixed, but it's not a
    miracle yet. i think real tuning it up will only make sense with real
    tape tests.
    [bitstream.cpp]
2023-08-11 downshifted to fm and 3300 hz
    seems to work ~275cps net
    naiive loop works in offline tests but seems to be less robust on
    hardware. delay-locked loop is still the most robust.
2023-08-14 tape sector overwrite experiment in progress
    pipico ded, working on the new pcb instead
    [tapeshnik-proto.kicad_pcb]
2023-08-20 schematic updated and boards sent for fab
    [bom.csv, designators.csv, positions.csv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]
2023-08-20 pcb layout
2023-08-20 12v paranoid
2023-09-01 kicad files for the mecha and motor controller
    [foc.kicad_pcb, foc.kicad_sch, platen-heads-butter.kicad_pcb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]
2023-09-03 adding a lot of mecha-specific stuff
    [bracket-l.stl, bracket-r.stl, foc.kicad_pcb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]
2023-10-01 updated schematics
    [foc.kicad_sch, tapeshnik-proto.kicad_pcb, tapeshnik-proto.kicad_sch]
2023-10-01 power sequencer switch circuit picture
2023-10-02 colourful printing of sector info
2023-10-02 succesfully replaced a sector
    [bitstream.cpp, config.h, tapeshnik.cpp]
2023-10-02 encoding was weirded, hopefully fixed
    stuff seems more steady now, need more verification
    current speed seems too fast, there are errors. but it's cool
    [bitstream.cpp, config.h]
2023-10-03 fine working stuff before complete teardown
    new version will have fixed sectors
    [bitstream.cpp, config.h]
2023-10-11 kicad file updates
    [foc.kicad_sch, platen-heads.kicad_pcb]
2023-10-11 updated 12v circuit
2023-10-12 reading retries continued
    some scan loop optimisations, some retry fixes
    next: data interleave and random seeks
    [bitstream.cpp, config.h, tapeshnik.cpp]
2025-12-08 updates kicad files + doc
    [foc.kicad_sch, pwm3389_pcb_edge.kicad_pcb, pwm3389_pcb_edge.kicad_sch]

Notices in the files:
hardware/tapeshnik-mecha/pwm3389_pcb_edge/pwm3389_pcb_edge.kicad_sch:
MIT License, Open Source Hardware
